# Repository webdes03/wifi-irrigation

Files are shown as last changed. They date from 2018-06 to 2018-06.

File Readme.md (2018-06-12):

*Disclaimer: This project is intended for users that understand basic electronics and wiring. No warranty is included, use at your own risk.*

# Wifi-Irrigation Introduction

Wifi-Irrigation allows for the control of up to four sprinkler valves using [SmartThings](https://smartthings.com) and a [Particle Photon](https://www.particle.io/). The build guide and parts list below are based on my build containing two sprinkler valves, but could be easily extended to support up to 4 valves/zones. Additional information, including a complete build guide is available at https://mike-greene.com/wifi-irrigation.

# Build Guide
## Table of Contents
- [Parts List](https://github.com/webdes03/wifi-irrigation#parts-listparts-list)
- [Assembly](https://github.com/webdes03/wifi-irrigation#parts-list#assembly)
    - [Manifold](https://github.com/webdes03/wifi-irrigation#manifold-1)
    - [Controller](https://github.com/webdes03/wifi-irrigation#controller-1)

## Parts List
### Controller
- [1x IP66 Rated Enclosure](https://amzn.to/2JEnlpK)
- [1x 3-Outlet Grounded Adapter](https://amzn.to/2Jrt92P)
- [1x U.FL Mini PCI to RP-SMA Antenna Pigtail](https://amzn.to/2JzkVZx)
- [1x 7dBi RP-SMA Wifi Antenna](https://amzn.to/2sQhzqG)
- [1x 7-Pin Waterproof Connector](https://amzn.to/2sNkyAn)
- [1x Orbit 24VAC Transformer](https://www.amazon.com/gp/product/B000VRYVYS/ref=oh_aui_detailpage_o00_s00?ie=UTF8&psc=1)
- [1x Particle Relay Shield](https://amzn.to/2kX4yZ2)
- [1x Particle Photon](https://amzn.to/2M9oNz7)
- [1x 12VDC, 2A Power Adapter](https://amzn.to/2Lxrr0i)
- [1x 20' Outdoor Extension Cord](https://amzn.to/2JkcsKH)
- [1x PG9 Waterproof Cable Connector](https://amzn.to/2JB4mwp)
- [3x P3 Wire Nuts](https://amzn.to/2MatAQO)
- [2x Pipe Strap](https://amzn.to/2Jy9y0S)

### Manifold
- [1x Garden Reel Leader Hose)](https://amzn.to/2JB5eRH)
- [2x 3/4" Sprinkler Valve](https://amzn.to/2Jnc51C)
- [2x Rain Bird Drip Irrigation 4-Port Manifold](https://amzn.to/2sPvNrY)
- [1x 3/4" Garden Hose to 1/2" PVC Adapter](https://www.pvcfittingsonline.com/3-4-x-1-2-pvc-garden-hose-adapter-male-mht-x-slip-mht101.html)
- [2x 90° Elbow Connector, 1/2" Schedule 40 PVC Fitting](https://www.pvcfittingsonline.com/406-005-1-2-schedule-40-pvc-90-ell.html)
- [1x Tee Connector, 1/2" Schedule 40 PVC Fitting](https://www.pvcfittingsonline.com/1-2-schedule-40-pvc-tee-socket-x-socket-x-socket-401-005.html)
- [2x 3/4" MIPT to PVC Adapter](https://www.pvcfittingsonline.com/436-007-3-4-schedule-40-pvc-male-adapter.html)
- [2x 3/4" to 1/2" Reducer Bushing](https://www.pvcfittingsonline.com/437-101-3-4-x-1-2-schedule-40-pvc-reducer-bushing-flush-style.html)
- [2x 3/4" to 1/2" Threaded Reducer Bushing](https://www.pvcfittingsonline.com/439-101-3-4-x-1-2-schedule-40-pvc-reducer-bushing-flush-style.html)
- [2x 1/2" x 1-1/2" Nipple](https://www.pvcfittingsonline.com/1-2-1-1-2-galvanized-malleable-nipple-mnpt-gsn12112.html)
- [5x 1/2" PVC Pipe cut to 2" in length](https://www.pvcfittingsonline.com/4004-005ab-1-2-schedule-40-pvc-pipe-5-ft-section.html)
- [PVC Primer & Cement](https://www.pvcfittingsonline.com/oatey-pvc-cement-primer-handy-pack-1-4-pints.html)
- [Teflon/PTFE Tape](https://amzn.to/2JwpgJF)

### Irrigation Components
- [1/4" Rain Bird Distribution Tubing](https://amzn.to/2kSmjsi)
- Assorted Drip Irrigation Emitters

## Assembly
### Manifold

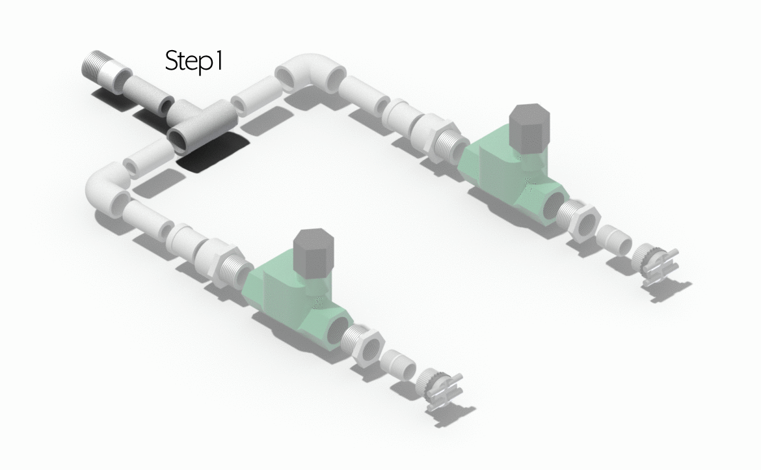
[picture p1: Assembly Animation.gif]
Assembly Animation


1.	Using one of your pieces of 2” PVC, connect the garden hose adapter to one end, and the tee connector to the other.
2.	With another piece of 2” PVC, connect an elbow connector to one side, and insert the other side into one of the 3/4" to 1/2" reducers (this is the reducer without any threads). Then insert the end with the reducer into one of the 3/4" to MIPT threaded adapters (which will later screw into one of the valves). Repeat this step so we have a second one for the second valve.
3.	Take one of the 1/2" x 1-1/2” nipples, and screw one side into one of the 3/4" to 1/2” threaded reducer bushing. Screw one of the 4-port drip irrigation manifolds onto the other side of the nipple. Repeat this step so we have a second one for the second valve.
4.	With one of the valves, connect one of the elbow subassemblies to the source side of the valve (as noted by the direction of the arrow). Connect one of the 4-port manifold subassemblies to the output side of the valve. Repeat this step with the second valve.
5.	Lastly, using the two remaining 2” pieces of PVC, connect the elbow ends of the valve subassemblies to each side of the tee connector.

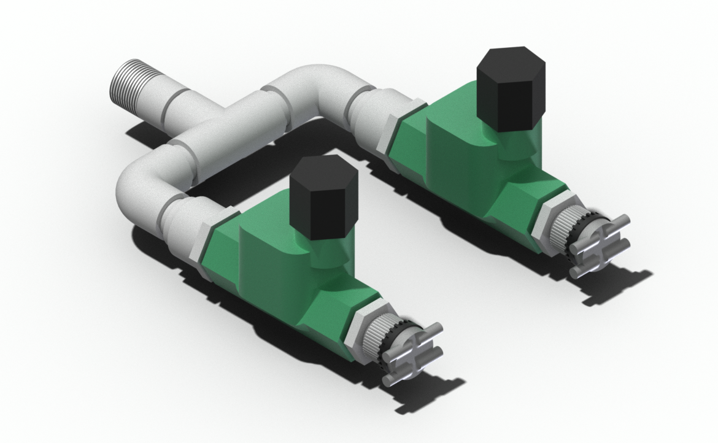
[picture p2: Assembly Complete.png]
Assembly Complete


### Controller

1.  Start by drilling all of the holes in the waterproof enclosure. You'll need to drill a hole for the PG9 connector, one for the RP-SMA antenna connector, one for the 7-pin waterproof connector, and 4 holes for the pipe straps to mount the manifold to the enclosure.
2.  Mount the PG9 connector, RP-SMA antenna connector, and 7-pin waterproof connector.
3.  Using 4 machine screws with lock washers, mount the manifold to the top of the controller box using two pipe straps, being sure to place silicon sealant around the inside of the bolts to help ensure the waterproofing of the box.
4.  Cut your extension cord, approximately 2 feet from the female end, and thread the male end through the PG9 connector. Clamp down the outside of the connector, then strip and reconnect the two ends of the extension cord. Cap the wires with wire nuts. Connect the 3-outlet grounded adapter to the female end of the extension cord inside the enclosure. Connect the 24VAC transformer and 12VDC transformer to the 3-outlet adapter.
5.  Solder the valve wires to the male end of the 7-pin waterproof connector. I used pins 1/2 for valve 1 and 3/4 for valve 2. Also solder 4 wires to the matching pins of the female side of the 7-pin connector, and wire them (along with the 24VAC transformer) as shown in the schematic below. We'll use the "MAIN" (center) terminal on the relay and the "NO" (normally open) side of the relay to control the valves.
6.  Connect the 12VDC transformer's barrel jack to the connector on the relay shield, and insert the Particle Photon into its place on the relay shield.
7.  Connect the pigtail from the u.Fl to RP-SMA antenna connector to the u.Fl connector on the Particle Photon, and screw the external wifi antenna to the lid of the enclosure.
8.  Lastly, use a piece of double-sided tape to mount the relay shield to the underside of the enclosure's lid.

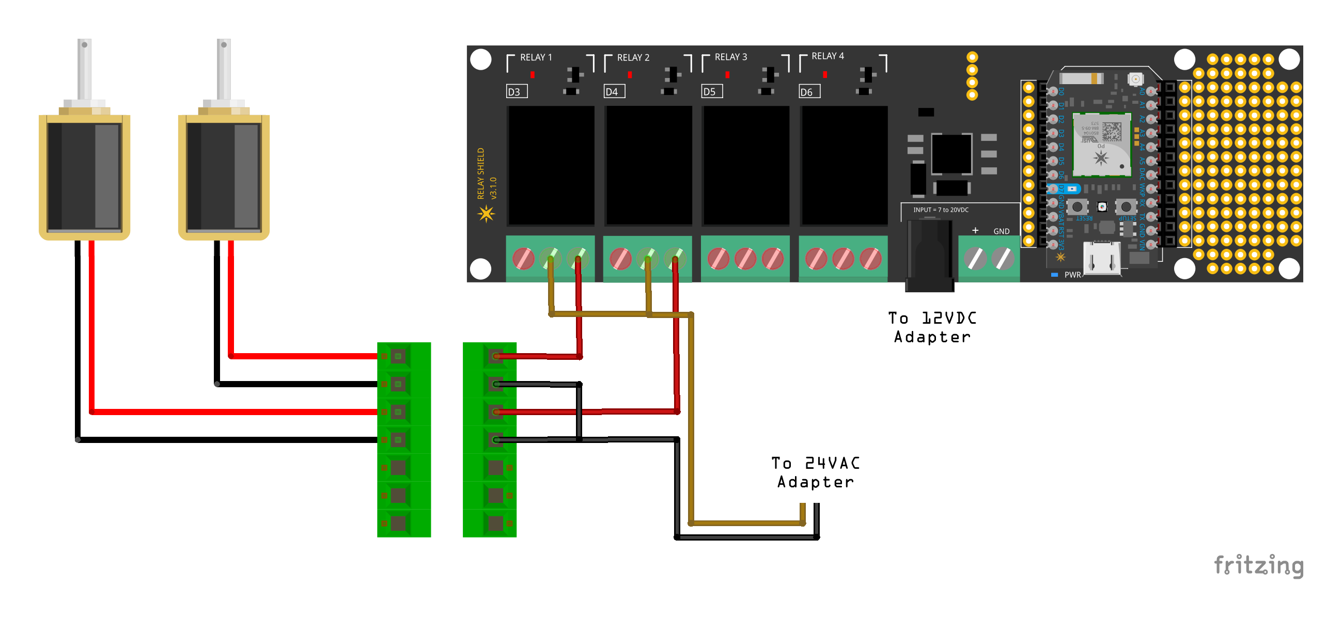
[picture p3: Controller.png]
Schematic


## Software & Automation

### Particle Setup
1.  Create a new Particle App
2.  Paste the contents of the [Particle Photon sketch](https://github.com/webdes03/wifi-irrigation/blob/master/wifi-irrigation.ino) into the IDE's code window, and save the app as "wifi-irrigation".
3.  Click the "Libraries" icon at the bottom left of the screen, and include the "RelayShield" library in the project by selecting it, then clicking the blue "Include in Project" button, then select the "wifi-irrigation" app. Click the blue "Confirm" button to continue.
4.  Save the app, and click the checkmark icon to verify the sketch.
5.  Assuming no errors are discovered, click the devices icon at the lower left of the screen, click the star icon next to the Photon you wish to flash the code to, then click the lightening bolt at the top left corner to flash the code to the Photon.

### SmartThings Setup

#### Device Handler
Follow the steps below to manually import the wifi-irrigation device handler, or connect your SmartThings IDE to my SmartThings repo to install this device handler, or device handlers from other projects.

1.  Login to your SmartThings IDE by going to https://graph.api.smartthings.com.
2.  From the top navigation bar, select "My Device Handlers", then click "Create New Device Handler".
3.  Select the "From Code" tab, and paste the contents of the [wifi-irrigation SmartThings Device Type](https://github.com/webdes03/SmartThingsPublic/tree/master/devicetypes/webdes03/wifi-irrigation.src) into the box, then click the "Create" button.
4.  Click the "Publish" button at the top right.

#### Devices
1.  From the top navigation of the SmartThings IDE, select "My Devices".
2.  Click the "New Device" button.
3.  Enter a name for your valve (ie: Front Flower Beds), a device network id (this must be unique, so use something like "wifi-irrigation-1" where 1 is the number of the valve), and select "wifi-irrigation" at the bottom of the type list, then click the "Create" button.
4.  Select the device that you just created (ie: Front Flower Beds), and click the "edit" link in the preferences section.
5.  Enter the Device ID and Authorization Token that we noted when we setup the Photon, and the number of the valve/relay that this device is connected to, then click "Save".
6.  With the device created, and configured, you should now see it listed in the SmartThings app.

#### Automation

For a complete overview of the automation approach for this project, review the build guide at https://mike-greene.com/wifi-irrigation.

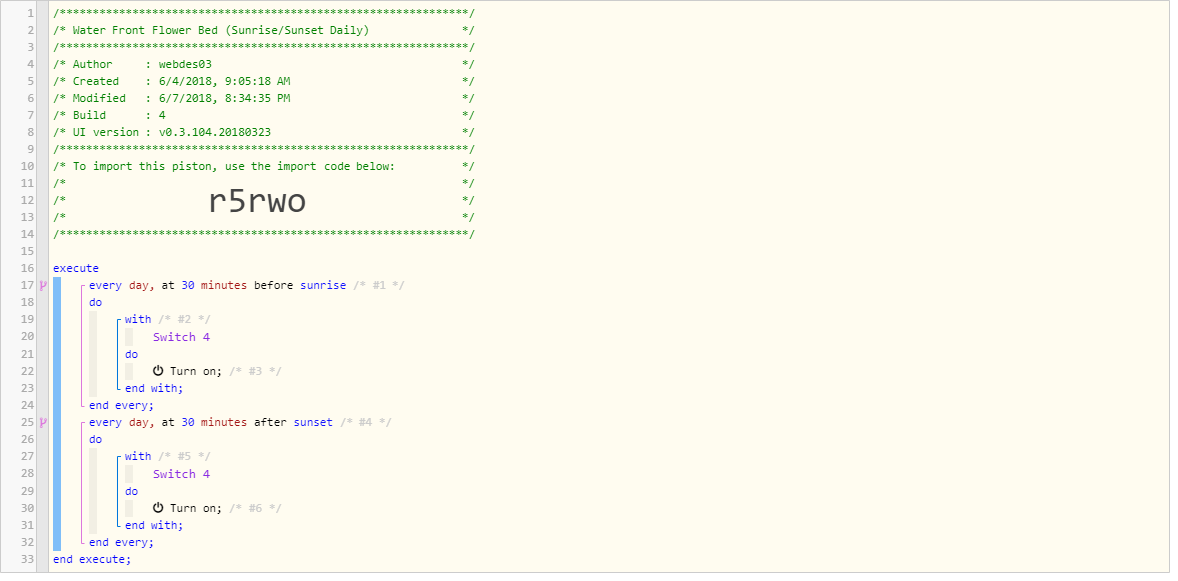
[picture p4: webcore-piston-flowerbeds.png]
Flower Beds

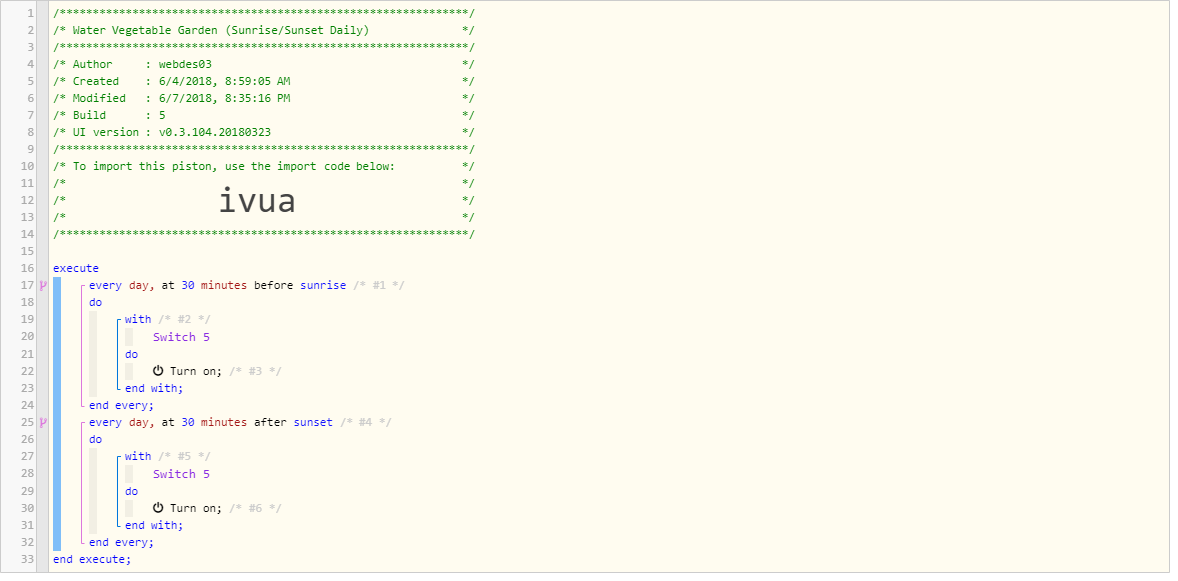
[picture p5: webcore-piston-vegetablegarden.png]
Vegetable Garden

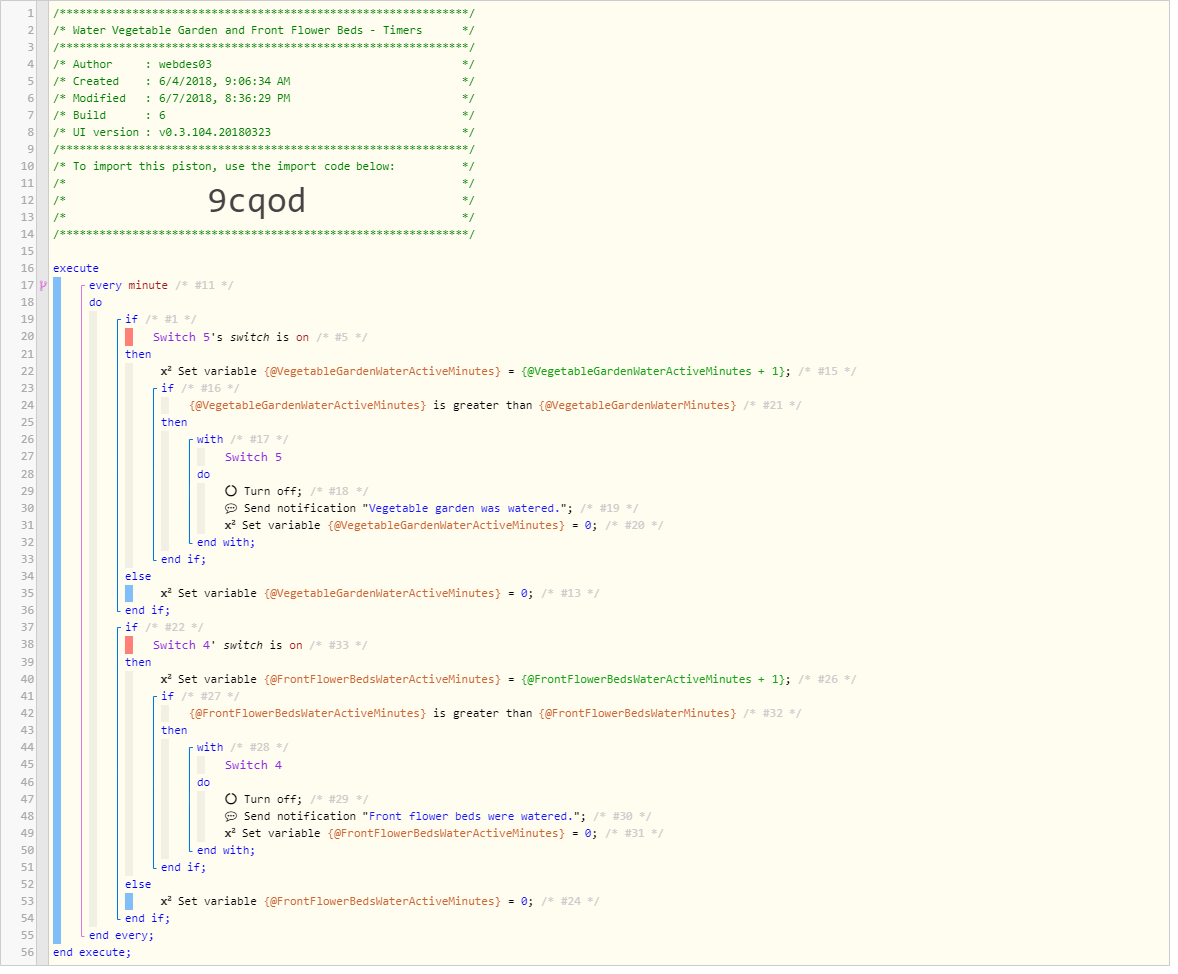
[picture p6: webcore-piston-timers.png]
Timers


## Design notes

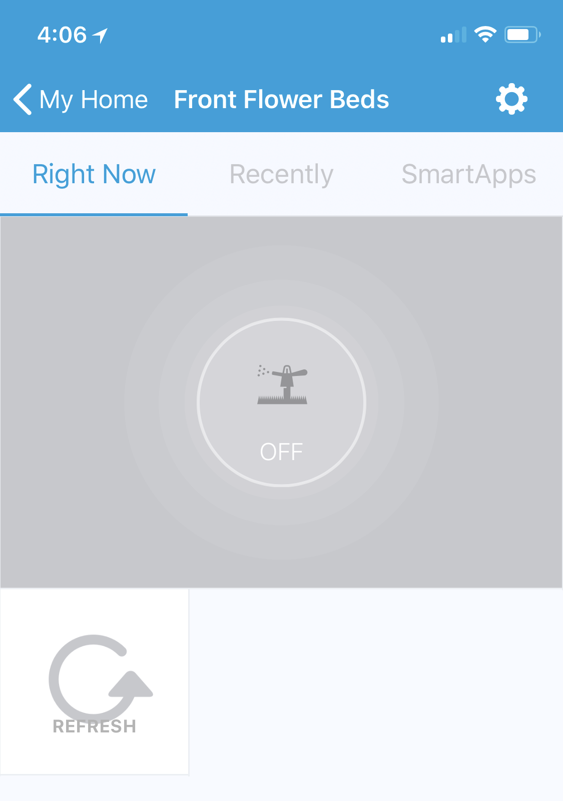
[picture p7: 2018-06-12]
smartthings-off.png

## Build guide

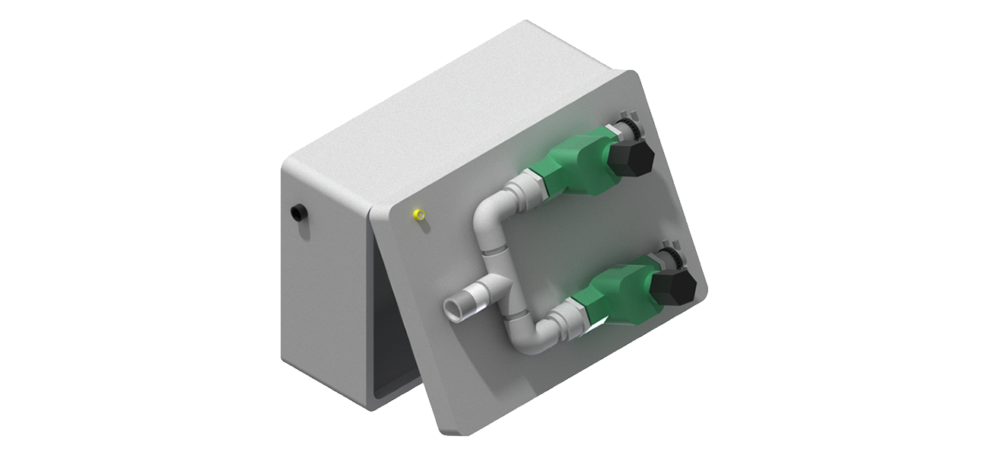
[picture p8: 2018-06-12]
Assembly.png

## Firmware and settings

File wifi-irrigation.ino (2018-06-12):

/*
wifi-irrigation project for Particle Photon
Copyright 2018 Michael Greene
https://mike-greene.com/wifi-irrigation

Licensed under the Apache License, Version 2.0 (the "License"); you may not use this 
file except in compliance with the License. You may obtain a copy of the License at:
http://www.apache.org/licenses/LICENSE-2.0
        
Unless required by applicable law or agreed to in writing, software distributed under 
the License is distributed on an "AS IS" BASIS, WITHOUT WARRANTIES OR CONDITIONS OF 
ANY KIND, either express or implied. See the License for the specific language governing 
permissions and limitations under the License.
*/

// This #include statement was automatically added by the Particle IDE.
#include "RelayShield.h"

// create an instance of the RelayShield library for the valves
RelayShield valveRelays;

// create function methods and an array to track relay state
int relayOn(String command);
int relayOff(String command);
int relayState[] = {0, 0, 0, 0, 0};

// select the u.FL antenna
STARTUP(WiFi.selectAntenna(ANT_EXTERNAL));

void setup() {
    valveRelays.begin();
    Particle.function("relayOn", relayOn);
    Particle.function("relayOff", relayOff);

    Particle.variable("valve1", &relayState[1], INT);
    Particle.variable("valve2", &relayState[2], INT);
    Particle.variable("valve3", &relayState[3], INT);
    Particle.variable("valve4", &relayState[4], INT);
}

void loop() {
    // nothing needed here, functions will run when called via the API
}

// define relayOn method
int relayOn(String command){
    Particle.publish("Valve On", command);
    
    // convert char command to valve integer
    char inputStr[64];
    command.toCharArray(inputStr,64);
    int i = atoi(inputStr);

    // turn the desired relay on
    valveRelays.on(i);
    relayState[i] = 1;

    // respond when successful
    return 1;
}

// define relayOff method
int relayOff(String command){
    Particle.publish("Valve Off", command);
    
    // convert char command to valve integer
    char inputStr[64];
    command.toCharArray(inputStr,64);
    int i = atoi(inputStr);

    // turn the desired relay off
    valveRelays.off(i);
    relayState[i] = 0;

    // respond when successful
    return 1;
}
